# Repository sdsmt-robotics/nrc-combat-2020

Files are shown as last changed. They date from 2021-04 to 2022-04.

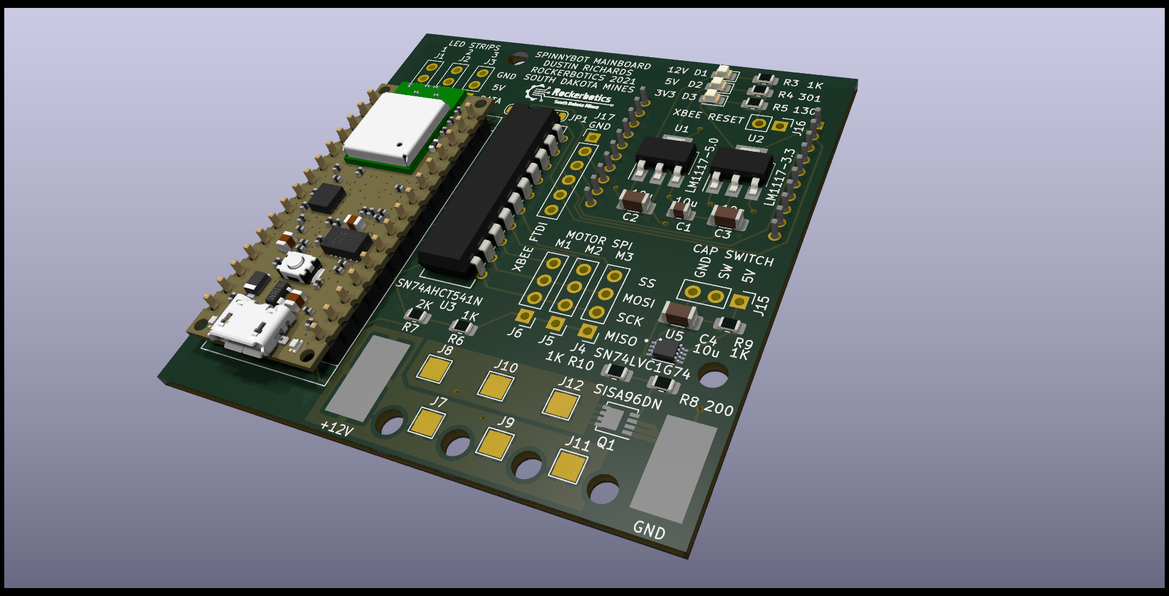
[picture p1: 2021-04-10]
spinnybot-motherboad/spinnybot-motherboad.png

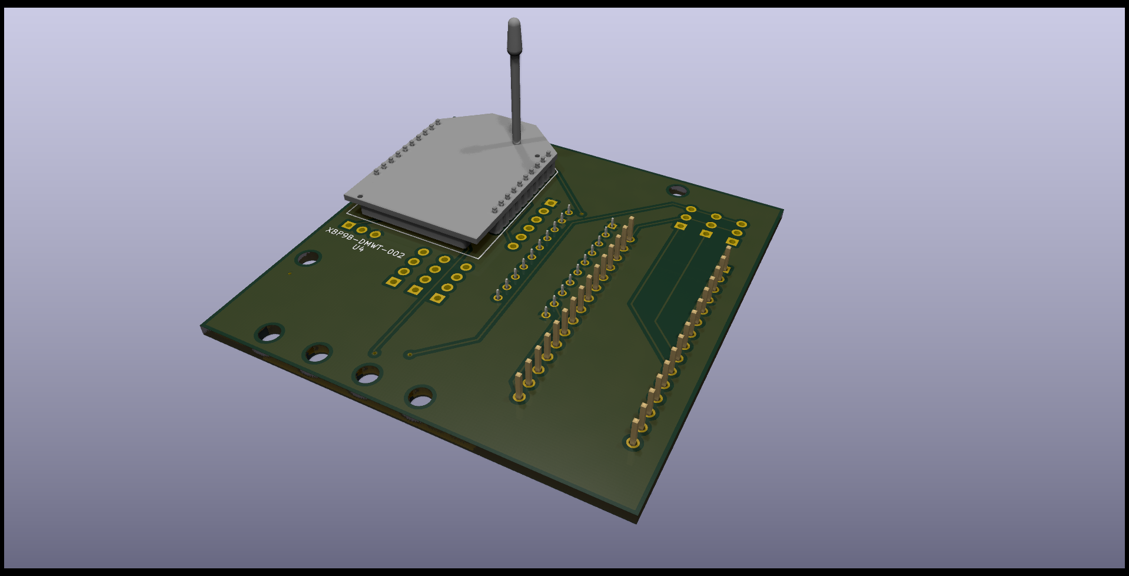
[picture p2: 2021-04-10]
spinnybot-motherboad/spinnybot-motherboad2.png

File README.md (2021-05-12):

# nrc-combat-2020
Robot code for the NRC Combat competition bot. Information about this bot can be found here: http://robotics.sdsmt.edu/projects/spinnybot  

# Hardware Info
This code is meant to run on an ESP32. It uses an ICM20649 Wide-Range 6-DoF IMU for orientation sensing. It also controls three NeoPixel 8x5050 RGB LED Sticks. For motor control, it interfaces with three Nidec24h motors controlled by our custom motor controller boards. For remote control, the bot receives commands from our custom remote controls over an xBee. The full system diagram is shown below.  

  

The main components of the control system (ESP32, xBee, voltage regulators, level shifters, etc) are held on a custom main board. The Kicad files for this are in the [spinnybot-motherboard](https://github.com/sdsmt-robotics/nrc-combat-2020/tree/master/spinnybot-motherboad) folder.  

# Software Info  
The main code for the bot is found in the [spinnybot-code](https://github.com/sdsmt-robotics/nrc-combat-2020/tree/master/spinnybot-code) folder. There are some additional arduino sketches for testing the various functionallities. These are found in the "testing" sub-folder. These tests run with the same libraries as the main control code.  

The pinouts are set up to run with the ESP32. But it should be able to run on any device with similar pin functionalities.  

## Required Libraries  
The required libraries are as follows:  
* Nidec24hController.h - Interface lib for the motor speed controller. Found [here](https://github.com/sdsmt-robotics/MotorSpeedController/tree/master/Software/controllerInterfaceLib).  
* Controller.h - Receive library for our custom remote control. Found [here](https://github.com/sdsmt-robotics/MotorSpeedController/tree/master/Software/controllerInterfaceLib).  
* FastLED.h - Code for interfacing with the LED strips. Install through the Arduino library manager.  
* Adafruit_ICM20649.h - Library for the ICM-20649 IMU. Install through the Arduino library manager.  

## Functionality  
The functionality is as follows. First, the bot will first initialize all peripherals. The LED strips are initialized first to show status throughout.Then the IMU is initialized. While this is occurring, the bot MUST remain stationary. The code runs through a calibration sequence each time, and any bumps will cause issues. During this stage the LEDs will show yellow, and will go green once complete. After, this the motors and remote control communications will be set up as well.  

For the main control loop, the bot has three main states:  
* No-spin: lights will be purple and the bot will not be spinning. Driver can drive the bot around with standard controls.  
* Spinny: bot is spinning with IMU feedback for orientation. LEDs will be red except when facing forward at which point they will be blue. Controls for driving are relative to "forward".  
* Full-spinny: lights will be red and bot will set all motors to full power. Feedback from IMU and attempts to drive will be ignored.

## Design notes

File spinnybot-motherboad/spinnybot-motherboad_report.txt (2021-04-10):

PCB statistics report
=====================
- Date: 3/25/2021 2:41:33 AM
- Project: spinnybot-motherboad
- Board name: spinnybot-motherboad

Board
-----
- Width: 63.5000 mm
- Height: 63.5000 mm
- Area: 4032.2500 sq. mm

Pads
----
- Through hole: 102
- SMD: 69
- Connector: 0
- NPTH: 6

Vias
----
- Through vias: 10
- Blind/buried: 0
- Micro vias: 0

Components
----------

| | Front Side | Back Side | Total |
|---|---|---|---|
|THT: | 12  | 1  | 13  |
|SMD: | 23  | 0  | 23  |
|Total:  | 35  | 1  | 36  |
| | | | |

Drill holes
-----------

| Count | Shape | X Size | Y Size | Plated | Via/Pad | Start Layer | Stop Layer |
|---|---|---|---|---|---|---|---|
| 186 | Round | 1.0000 mm | 1.0000 mm | PTH | Pad | F.Cu | B.Cu |
| 60 | Round | 0.7874 mm | 0.7874 mm | PTH | Pad | F.Cu | B.Cu |
| 60 | Round | 0.8000 mm | 0.8000 mm | PTH | Pad | F.Cu | B.Cu |
| 30 | Round | 0.4000 mm | 0.4000 mm | PTH | Via | F.Cu | B.Cu |
| 18 | Round | 3.0000 mm | 3.0000 mm | NPTH | Pad | F.Cu | B.Cu |

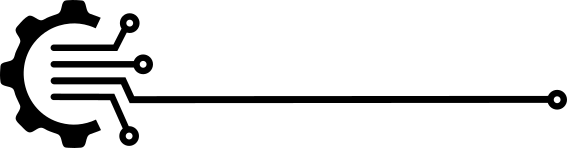
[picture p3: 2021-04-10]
spinnybot-motherboad/art6/.svg2shenzhen-cache/images/F.Mask_g1609.png

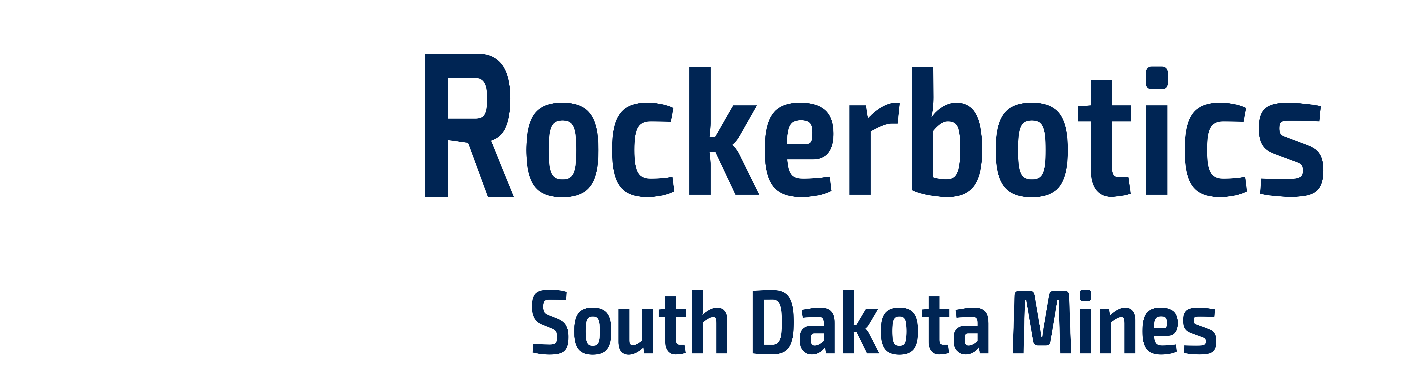
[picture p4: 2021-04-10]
spinnybot-motherboad/art4/.svg2shenzhen-cache/images/F.SilkS_layer2.png

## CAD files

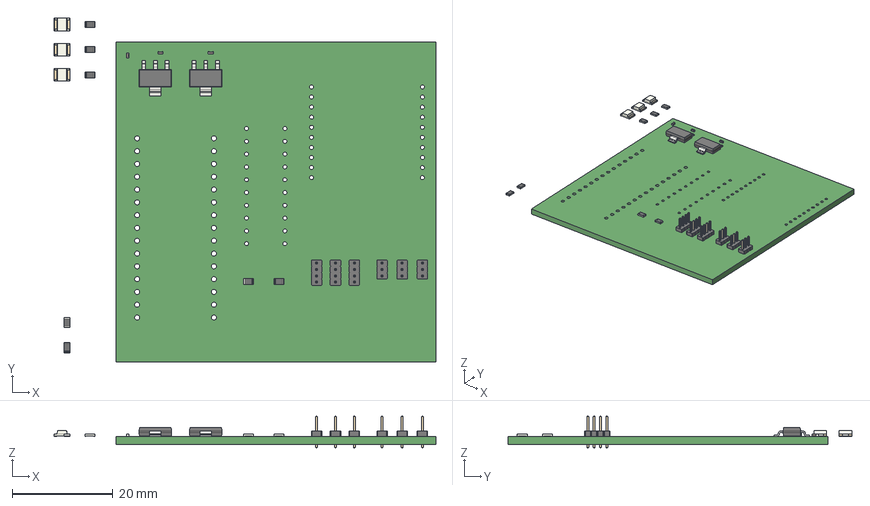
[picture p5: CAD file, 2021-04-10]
spinnybot-motherboad/spinnybot-motherboad.step
75.8 x 68.2 x 6.30 mm

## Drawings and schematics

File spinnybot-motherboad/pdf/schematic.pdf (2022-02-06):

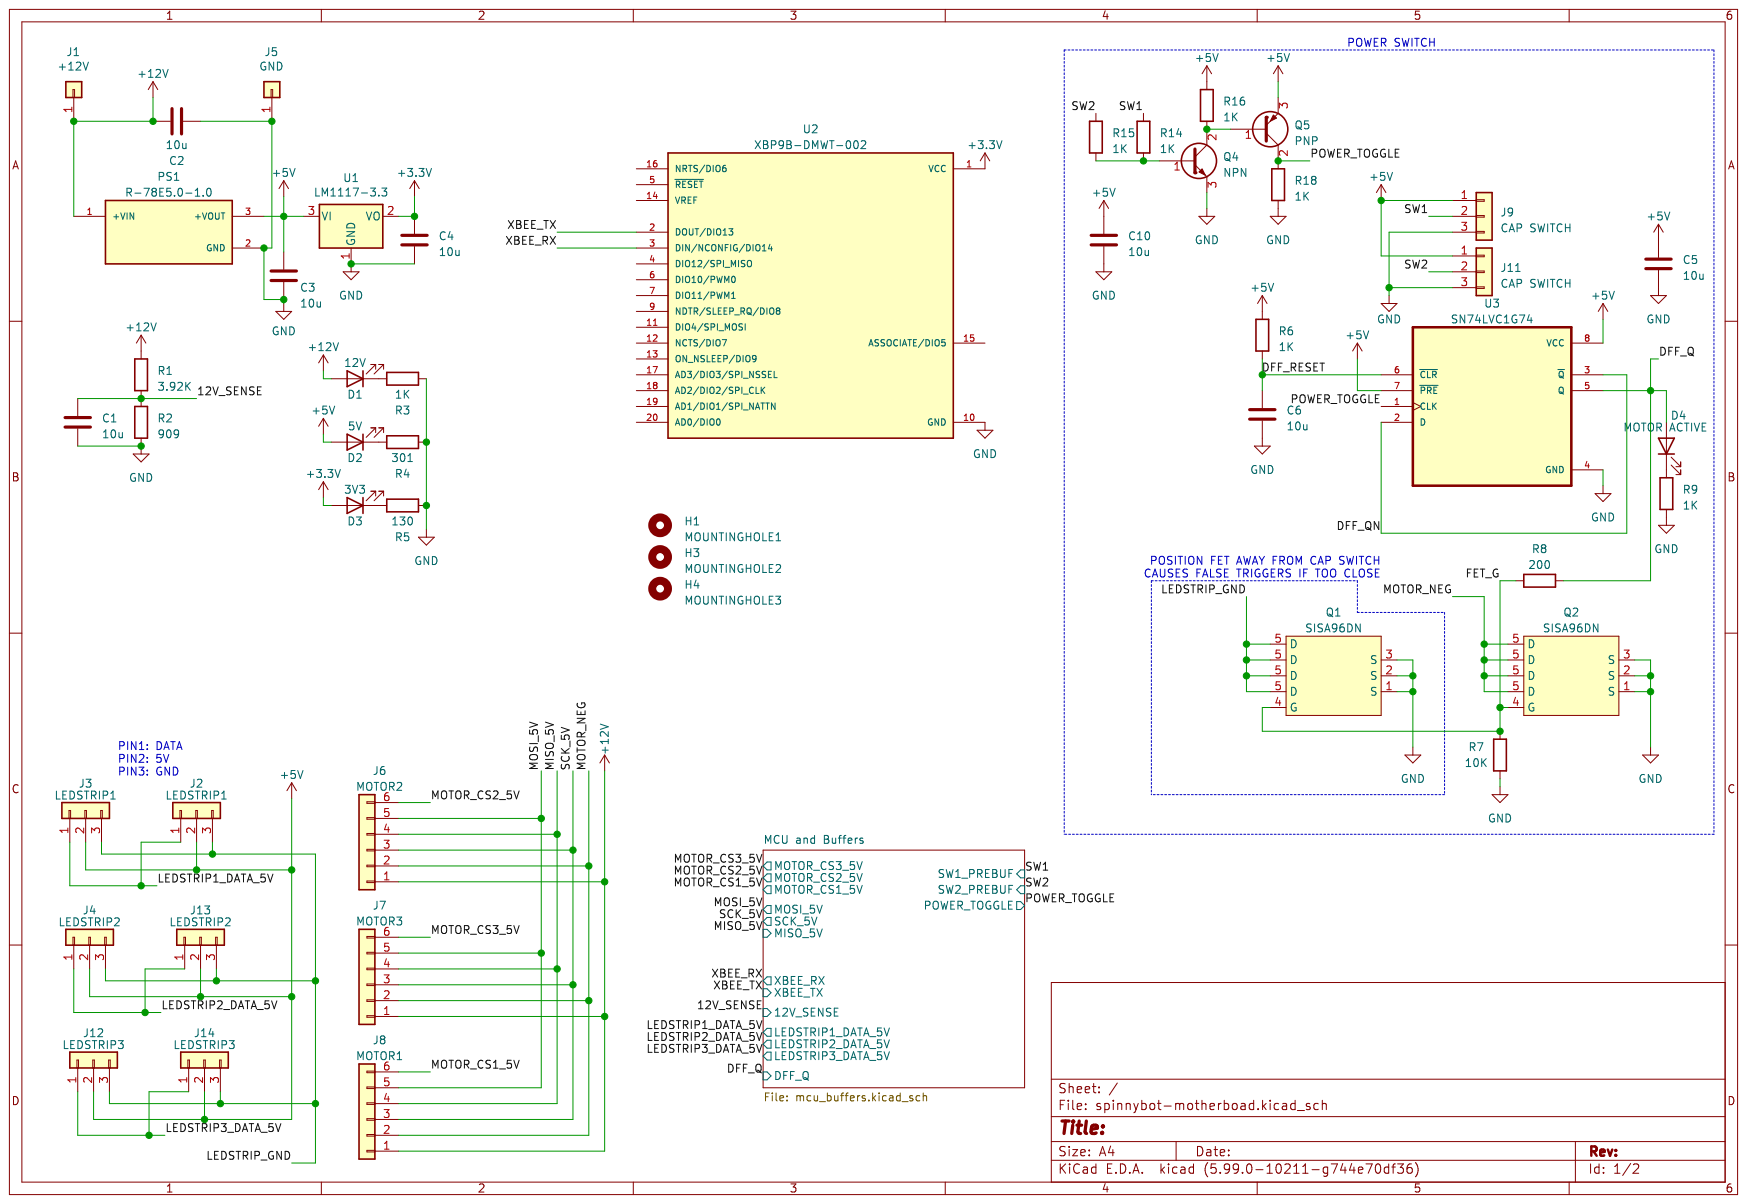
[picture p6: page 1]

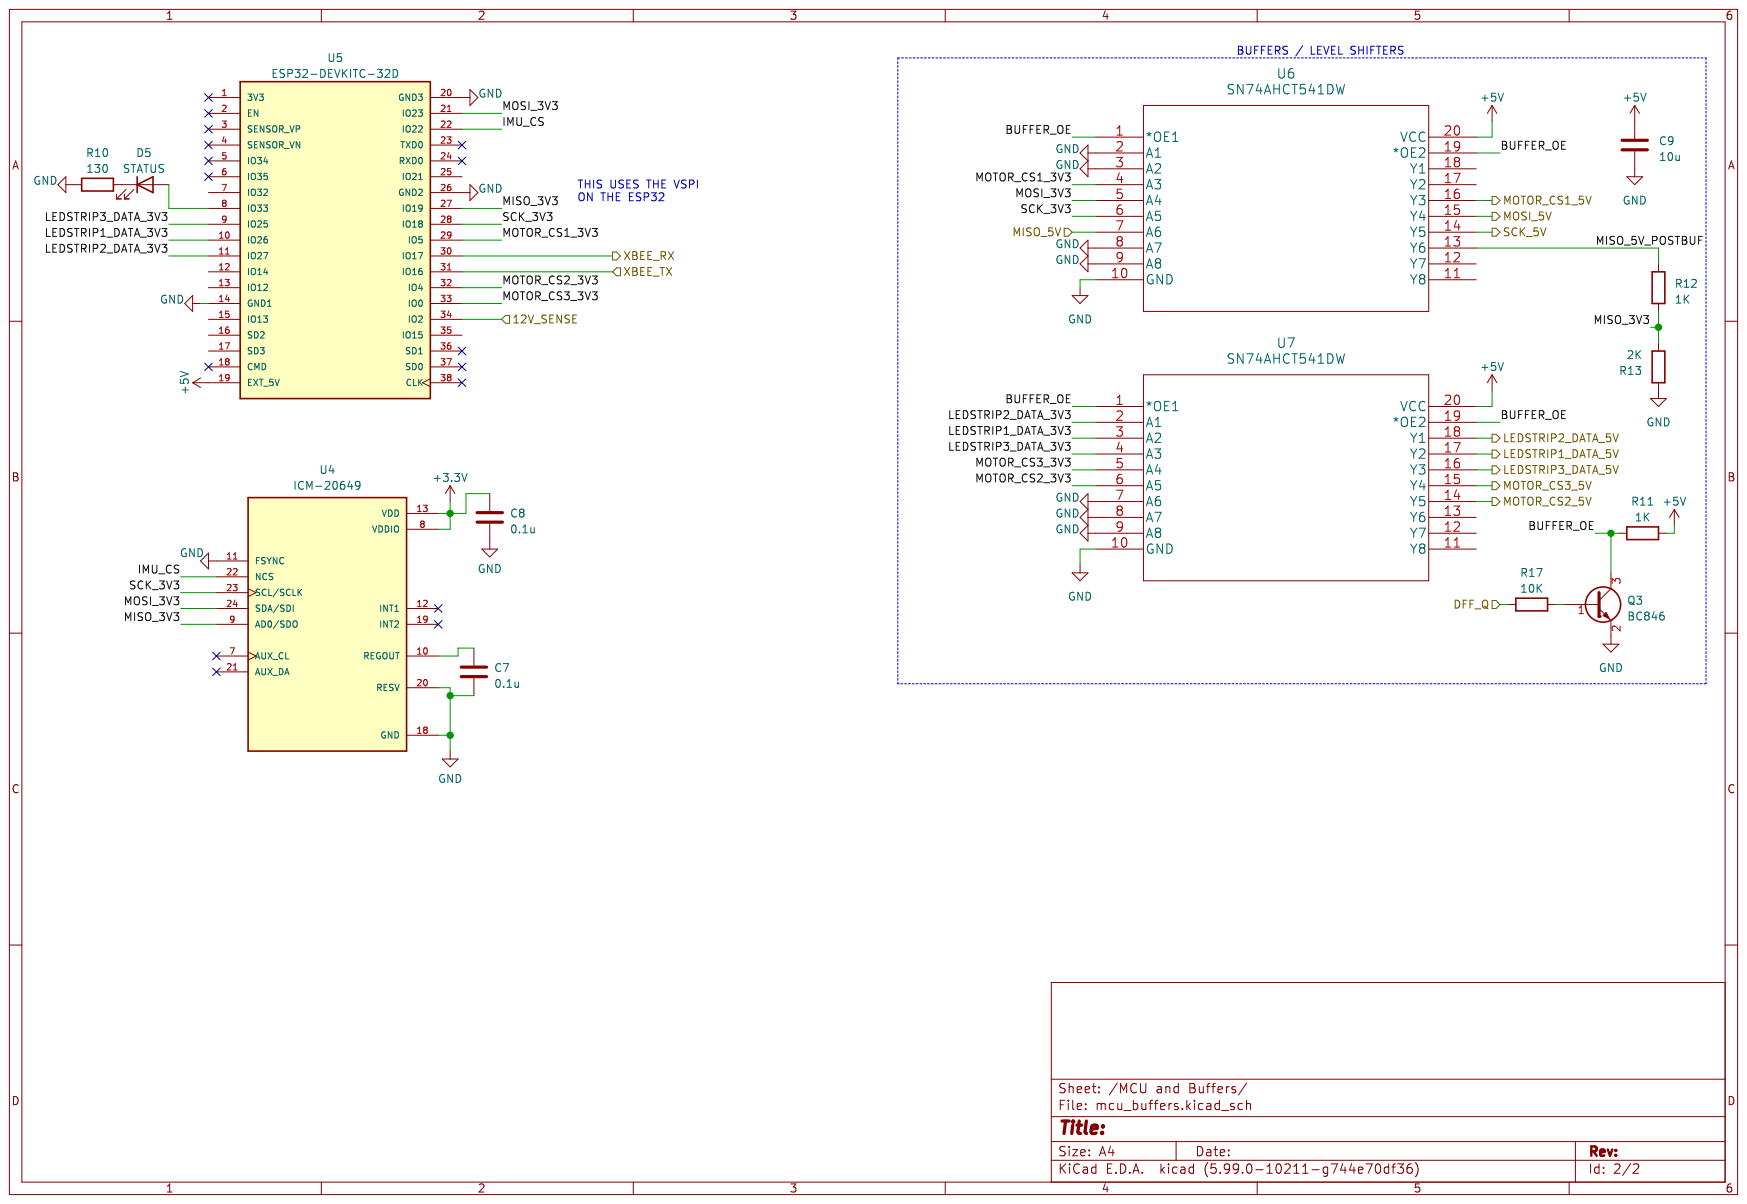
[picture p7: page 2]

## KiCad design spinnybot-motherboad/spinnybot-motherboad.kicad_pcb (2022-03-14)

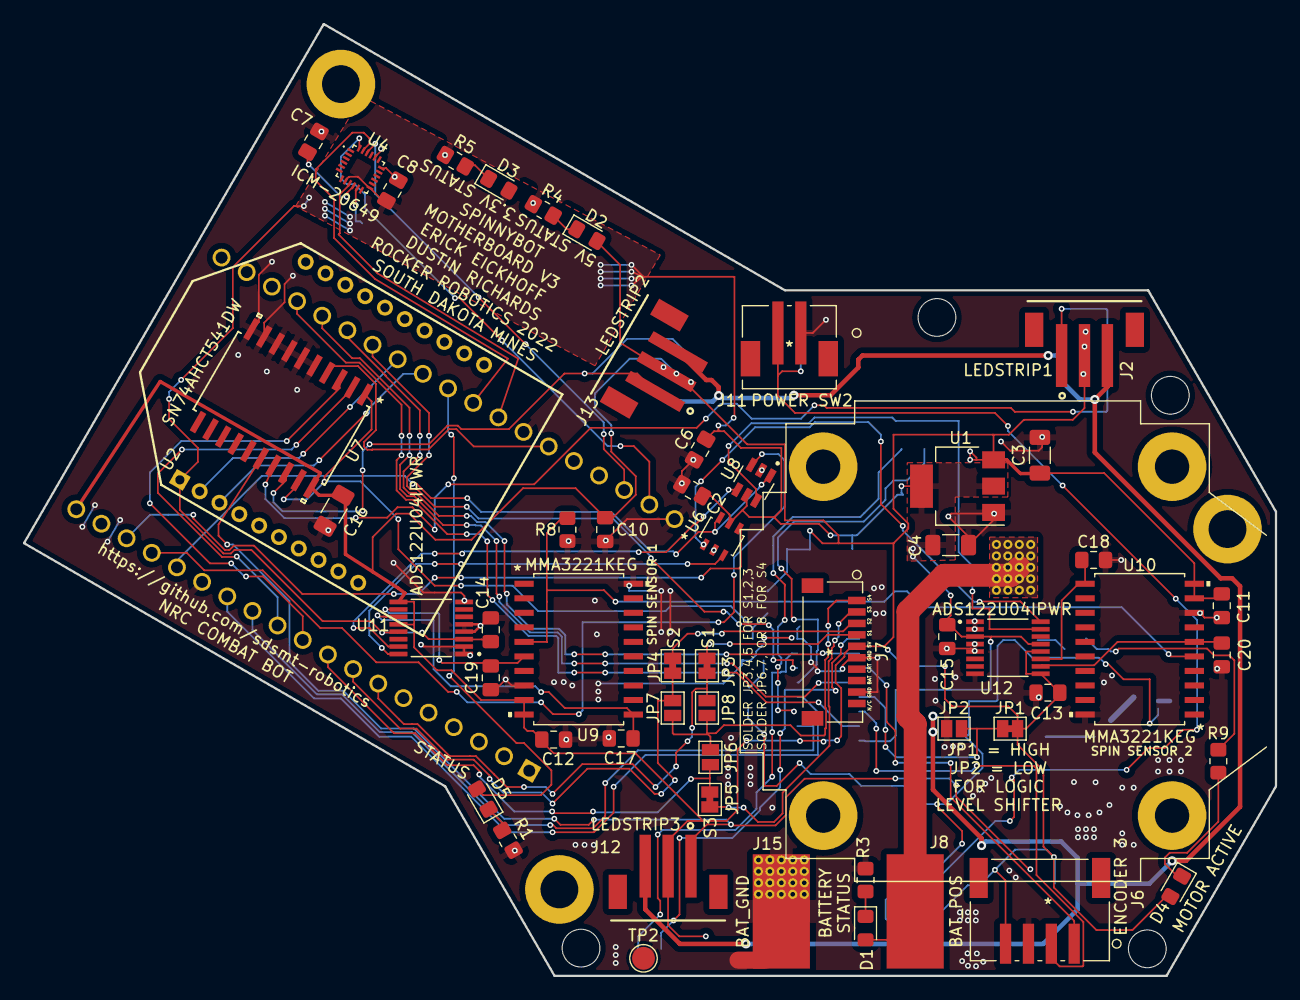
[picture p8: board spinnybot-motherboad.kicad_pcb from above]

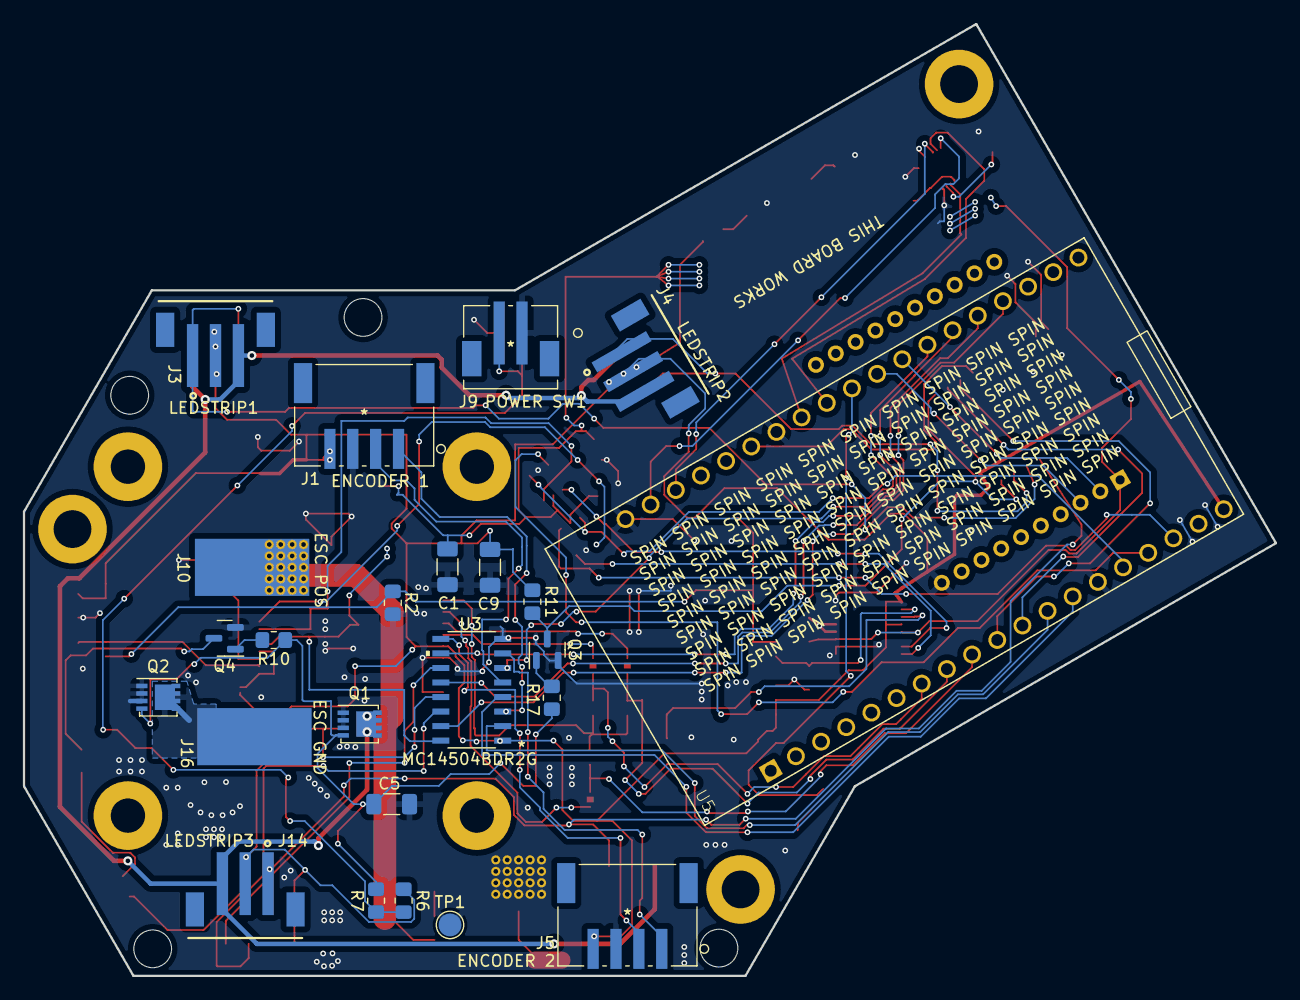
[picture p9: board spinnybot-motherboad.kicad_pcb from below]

Board: 2 copper layers, 109.4 x 83.2 mm, 87 parts (24 on the bottom side), 63 nets.

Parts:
A1: ESC_Hobbywing_X-Rotor_Micro_60A_4in1
C1, C3, C4, C5, C9: 10u; C_1206_3216Metric_Pad1.33x1.80mm_HandSolder
C2, C6, C7, C8, C10, C11, C12, C13, C14, C15: 0.1u; C_0805_2012Metric_Pad1.18x1.45mm_HandSolder
C16: 0.1u; C_1206_3216Metric_Pad1.33x1.80mm_HandSolder
C17, C18, C19, C20: 10nF; C_0805_2012Metric_Pad1.18x1.45mm_HandSolder
D1: 12V; LED_0805_2012Metric_Pad1.15x1.40mm_HandSolder
D2: 5V; LED_0805_2012Metric_Pad1.15x1.40mm_HandSolder
D3: 3V3; LED_0805_2012Metric_Pad1.15x1.40mm_HandSolder
D4: MOTOR ACTIVE; LED_0805_2012Metric_Pad1.15x1.40mm_HandSolder
D5: STATUS; LED_0805_2012Metric_Pad1.15x1.40mm_HandSolder
H1: MOUNTINGHOLE1; MountingHole_3.3mm
H2, H7: STRAINHOLE1; StrainHole_3.3mm
H3: MOUNTINGHOLE2; MountingHole_3.3mm
H4: MOUNTINGHOLE3; MountingHole_3.3mm
H6: STRAINHOLE3; StrainHole_3.3mm
H8: STRAINHOLE2; StrainHole_3.3mm
J1: ENCODER 1; S4B-PH-SM4-TBLFSN
J2, J3: LEDSTRIP1; JST_B3B-PH-SM4-TB(LF)(SN)
J4, J13: LEDSTRIP2; JST_B3B-PH-SM4-TB(LF)(SN)
J5: ENCODER 2; S4B-PH-SM4-TBLFSN
J6: ENCODER 3; S4B-PH-SM4-TBLFSN
J7: SM10B-SRSS-TB
J8: BAT_POS; SolderWirePad_1x01_SMD_5x10mm
J9: POWER SW1; B2B-PH-SM4-TBLFSN
J10: ESC_POS; Stitched_SolderWirePad_1x01_SMD_5x10mm
J11: POWER SW2; B2B-PH-SM4-TBLFSN
J12, J14: LEDSTRIP3; JST_B3B-PH-SM4-TB(LF)(SN)
J15: BAT_GND; Stitched_SolderWirePad_1x01_SMD_5x10mm
J16: ESC_GND; SolderWirePad_1x01_SMD_5x10mm
JP1, JP3, JP4, JP5: SolderJumper_2_Bridged; SolderJumper-2_P1.3mm_Bridged_Pad1.0x1.5mm
JP2, JP6, JP7, JP8: SolderJumper_2_Open; SolderJumper-2_P1.3mm_Open_Pad1.0x1.5mm
Q1, Q2: SISA96DN; Vishay_PowerPAK_1212-8_Single
Q3, Q4: BC846; SOT-23
R1, R5: 130; R_0805_2012Metric_Pad1.20x1.40mm_HandSolder
R2, R8: 10k; R_0805_2012Metric_Pad1.20x1.40mm_HandSolder
R3, R11: 1K; R_0805_2012Metric_Pad1.20x1.40mm_HandSolder
R4: 301; R_0805_2012Metric_Pad1.20x1.40mm_HandSolder
R6: 1k; R_0805_2012Metric_Pad1.20x1.40mm_HandSolder
R7: 150k; R_0805_2012Metric_Pad1.20x1.40mm_HandSolder
R9: 220; R_0805_2012Metric_Pad1.20x1.40mm_HandSolder
R10, R17: 10K; R_0805_2012Metric_Pad1.20x1.40mm_HandSolder
TP1, TP2: TestPoint; TestPoint_Pad_D2.0mm
U1: LM1117-3.3; SOT-223-3_TabPin2
U2: XBP9B-DMWTB002; DIP2200W51P200L3294H279Q20P
U3: MC14504BDR2G
U4: ICM-20649; QFN40P300X300X95-24N
U5: ESP32-DEVKITC-32D; MODULE_ESP32-DEVKITC-32D
U6: 74LVC1G157GV_125
U7: SN74AHCT541DW
U8: SN74LVC1G18DBVR; SOT95P280X145-6N
U9, U10: MMA3221KEG
U11, U12: ADS122U04IPWR; SOP65P640X120-16N

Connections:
+3V3: C1.1, C2.1, C4.1, C6.1, C8.1, C14.1, C15.1, D3.2 (A), U1.2 (VO), U2.1 (VCC), U3.16 (VDD), U4.8 (VDDIO), U4.13 (VDD), U6.5 (VCC), U8.5 (VCC), U11.3 (RESET_N), U11.13 (DVDD), U12.3 (RESET_N), U12.13 (DVDD)
+5V: C3.1, C9.1, C10.1, C11.1, C12.1, C13.1, C16.1, D2.2 (A), D4.2 (A), J1.4, J2.2, J3.2, J4.2, J5.4, J6.4, J7.5, J12.2, J13.2, J14.2, JP1.2 (B), R6.1, R11.1, U1.3 (VI), U3.1 (VCC), U5.19 (EXT_5V), U7.20 (VCC), U9.9 (VDD), U9.10 (AVDD), U10.9 (VDD), U10.10 (AVDD), U11.9 (REFP), U11.12 (AVDD), U12.9 (REFP), U12.12 (AVDD)
+12V: D1.2 (A), J8.1, J10.1
/ACCEL_SELF_TEST: R2.1, R8.1, U9.5 (ST), U10.5 (ST)
/ADC_RX: U5.17 (SD3), U6.4 (Y)
/ADC_SEL: U5.15 (IO13), U6.6 (S), U8.1 (S)
/ADC_TX: U5.16 (SD2), U8.3 (A)
/Connectors/ESC_S4: J7.1, JP6.1 (A), JP7.1 (A), JP8.1 (A)
/ENC_1A_5V: J1.1, U3.3 (AIN)
/ENC_1B_5V: J1.2, U3.5 (BIN)
/ENC_2A_5V: J5.1, U3.7 (CIN)
/ENC_2B_5V: J5.2, U3.9 (DIN)
/ENC_3A_5V: J6.1, U3.11 (EIN)
/ENC_3B_5V: J6.2, U3.14 (FIN)
/ESC_S1: JP3.2 (B), JP8.2 (B), U5.7 (IO32)
/ESC_S2: JP4.2 (B), JP7.2 (B), U5.8 (IO33)
/ESC_S3: JP5.2 (B), JP6.2 (B), U5.9 (IO25)
/IMU and Accelerometers/ADC1_RX: U6.3 (I0), U11.16 (RX)
/IMU and Accelerometers/ADC1_TX: U8.4 (Y1), U11.15 (TX)
/IMU and Accelerometers/ADC2_RX: U6.1 (I1), U12.16 (RX)
/IMU and Accelerometers/ADC2_TX: U8.6 (Y2), U12.15 (TX)
/IMU_CS: U4.22 (NCS), U5.22 (IO22)
/LEDSTRIP1_DATA_5V: J2.1, J3.1, U7.17 (Y2)
/LEDSTRIP2_DATA_5V: J4.1, J13.1, U7.18 (Y1)
/LEDSTRIP3_DATA_5V: J12.1, J14.1, U7.16 (Y3)
/LEDSTRIP_GND: J2.3, J3.3, J4.3, J12.3, J13.3, J14.3, Q1.5 (D)
/MCU and Buffers/BUFFER_OE: Q3.3 (C), R11.2, U7.1 (*OE1), U7.19 (*OE2)
/MCU and Buffers/ENC_1A_3V3: U3.2 (AOUT), U5.12 (IO14)
/MCU and Buffers/ENC_1B_3V3: U3.4 (BOUT), U5.13 (IO12)
/MCU and Buffers/ENC_2A_3V3: U3.6 (COUT), U5.32 (IO4)
/MCU and Buffers/ENC_2B_3V3: U3.10 (DOUT), U5.33 (IO0)
/MCU and Buffers/ENC_3A_3V3: U3.12 (EOUT), U5.34 (IO2)
/MCU and Buffers/ENC_3B_3V3: U3.15 (FOUT), U5.35 (IO15)
/MCU and Buffers/LEDSTRIP1_DATA_3V3: U5.10 (IO26), U7.3 (A2)
/MCU and Buffers/LEDSTRIP2_DATA_3V3: U5.11 (IO27), U7.2 (A1)
/MCU and Buffers/LEDSTRIP3_DATA_3V3: U5.25 (IO21), U7.4 (A3)
/MCU and Buffers/XBEE_RX: U2.3 (DIN/NCONFIG/DIO14), U5.30 (IO17)
/MCU and Buffers/XBEE_TX: U2.2 (DOUT/DIO13), U5.31 (IO16)
/MISO_3V3: U4.9 (AD0/SDO), U5.27 (IO19)
/MOSI_3V3: U4.24 (SDA/SDI), U5.21 (IO23)
/POWER_ON: C5.2, Q1.4 (G), Q2.4 (G), R7.2, R10.1, R17.2
/Power/ESC_GND: J16.1, Q2.5 (D)
/Power/POWER_SW_IN: J9.2, J11.2, R6.2, R7.1
/SCK_3V3: U4.23 (SCL/SCLK), U5.28 (IO18)
GND: C1.2, C2.2, C3.2, C4.2, C5.1, C6.2, C7.2, C8.2, C9.2, C10.2, C11.2, C12.2, C13.2, C14.2, C15.2, C16.2, C17.2, C18.1, C19.1, C20.1, J1.3, J5.3, J6.3, J7.6, J7.9, J9.1, J11.1, J15.1, JP2.1 (A), Q1.1 (S), Q1.2 (S), Q1.3 (S), Q2.1 (S), Q2.2 (S), Q2.3 (S), Q3.2 (E), Q4.2 (E), R1.1, R2.2, R3.1, R4.1, R5.1, R8.2, TP1.1, TP2.1, U1.1 (GND), U2.10 (GND), U3.8 (VSS), U4.11 (FSYNC), U4.18 (GND), U4.20 (RESV), U5.14 (GND1), U5.20 (GND3), U5.26 (GND2), U6.2 (GND), U7.5 (A4), U7.6 (A5), U7.7 (A6), U7.8 (A7), U7.9 (A8), U7.10 (GND), U8.2 (GND), U9.8 (VSS), U9.20 (GND), U10.8 (VSS), U10.20 (GND), U11.1 (GPIO1), U11.2 (GPIOO), U11.4 (DGND), U11.5 (AVSS), U11.8 (REFN), U12.1 (GPIO1), U12.2 (GPIOO), U12.4 (DGND), U12.5 (AVSS), U12.8 (REFN)
unnamed: C7.1, U4.10 (REGOUT)
unnamed: C17.1, U9.11 (YOUT), U11.11 (AINO)
unnamed: C18.2, U10.11 (YOUT), U12.11 (AINO)
unnamed: C19.2, U9.6 (XOUT), U11.10 (AIN1)
unnamed: C20.2, U10.6 (XOUT), U12.10 (AIN1)
unnamed: D1.1 (K), R3.2
unnamed: D2.1 (K), R4.2
unnamed: D3.1 (K), R5.2
unnamed: D4.1 (K), R9.2
unnamed: D5.1 (K), R1.2
unnamed: D5.2 (A), U5.29 (IO5)
unnamed: J7.2, JP5.1 (A)
unnamed: J7.3, JP4.1 (A)
unnamed: J7.4, JP3.1 (A)
unnamed: JP1.1 (A), JP2.2 (B), U3.13 (MODE)
unnamed: Q3.1 (B), R17.1
unnamed: Q4.1 (B), R10.2
unnamed: Q4.3 (C), R9.1

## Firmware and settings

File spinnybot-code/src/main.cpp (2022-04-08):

#include <Arduino.h>
#include <math.h>

// #include "accelerometer.h"
#include "constants.h"
#include "controller.h"
#include "driveFuncs.h"
#include "encoder.h"
#include "imu.h"
#include "led.h"
#include "motor.h"
#include "ota.h"
#include "pins.h"
#include "utility.h"

#define AP_SSID "SPINNY" // ssid for robot

// ---- SENSOR STUFF ----

IMU imu;

Encoder e1(ENC_1, 360);
Encoder e2(ENC_2, 360);
Encoder e3(ENC_3, 360);

/* Accelerometers accel(Serial1, ADC_SELECT, ADC_TX,
                     ADC_RX); // note: tx and rx are fliped
                     */

// ---- LED STUFF ----

LedStrip strip1(LED_STRIP_1);
LedStrip strip2(LED_STRIP_2);
LedStrip strip3(LED_STRIP_3);
LedStrip* strips[] = {&strip1, &strip2, &strip3};

// ---- MOTOR STUFF ----

Motor m1(MOTOR_1, MOTOR_1_RMT_CHANNEL);
Motor m2(MOTOR_2, MOTOR_2_RMT_CHANNEL);
Motor m3(MOTOR_3, MOTOR_3_RMT_CHANNEL);

const long MOTOR_UPDATE_INTERVAL = 10; // motor update loop time in microseconds
long last_motor_update = micros();

// ---- LOOP STUFF ----

bool robot_enabled = false;

const long LOOP_INTERVAL = 1000; // microsec
long last_loop = micros();

// ---- CONTROLLER STUFF ----

Controller controller(CONTROLLER_SERIAL);

// movement
// range -1 to 1, negative is reverse
float x = 0;
float y = 0;

// Offset for facing direction, FIXME need values for offset
float imu_offset = 0;

// spin speed
//  range -1 to 1, negative is reverse
float spin = 0;

bool flip = false;

bool full_send = false;

// variables

float body_angle = 0;

DriveManager driveManager;

// ---- SENSOR FUNCTIONS ----

/**
   @brief Initializes all sensors.
*/
void initSensors() {
  // init IMU
  if (!imu.init()) {
    Serial.println("\nimu fail init");
  }

  // init accelerometers
  // accel.init();

  // init encoders
  e1.init();
  e2.init();
  e3.init();
}

/**
   @brief Updates all sensors.
*/
void updateSensors() {
  // update IMU
  imu.update();

  // update accelerometers
  // accel.update();

  // update encoders
  e1.update();
  e2.update();
  e3.update();

  // Update values in drive manager
  float encVels[] = {e1.getUnfilteredSpeed(), e2.getUnfilteredSpeed(), e3.getUnfilteredSpeed()};
  driveManager.updateOrientation(imu.getRawVelocity(), encVels);

  //body_angle = imu.getAngle() + imu_offset;
}

// ---- MOTOR FUNCTIONS ----

/**
   @brief Initializes all motors.
*/
void initMotors() {
  m1.init();
  m2.init();
  m3.init();
}

/**
   @brief Sends a DShot command to all motors.
   @param cmd command
*/
void sendAllMotorCommand(int cmd) {
  m1.send_dshot_command(cmd);
  m2.send_dshot_command(cmd);
  m3.send_dshot_command(cmd);
}

/**
   @brief Sets a power for all motors.
   @param power power value to set. -1000 to 1000
*/
void sendAllMotorPower(int power) {
  m1.set_speed_signed(power);
  m2.set_speed_signed(power);
  m3.set_speed_signed(power);
}

/**
   @brief Arms all motors by initialy sending the 0 command and then sets the
   power to 0 for the initialization. This blocks for MOTOR_INIT_TIME
   miliseconds.
*/
void armMotors() {
  long init_motor_start = millis();
  sendAllMotorCommand(0);
  while (millis() - init_motor_start < MOTOR_INIT_TIME) {
    sendAllMotorPower(0);
  }
}

/**
   @brief Updates drive motor powers with control and angle inputs.
   @param spin Spin speed modifier. -1.0 to 1.0
   @param x X direction movement modifier. -1.0 to 1.0
   @param y Y direction movement modifier. -1.0 to 1.0
   @param angle Current angle of robot in radians
*/
void updateDrive(float spin, float x, float y) {
  // Calculate the power
  int power[3] = {0, 0, 0};
  driveManager.calcDrivePower(power, spin, x, y);

  // update motor power
  m1.set_speed_signed(power[0]);
  m2.set_speed_signed(power[1]);
  m3.set_speed_signed(power[2]);
}

// ---- LED FUNCTIONS ----

/**
   @brief Turns both status LEDs on and off
   @param on true = on, false = off
*/
void setStatusLED(bool on) {
  digitalWrite(STATUS_LED_PIN, on);
  digitalWrite(ESP_STATUS_LED_PIN, on);
}

/**
   @brief Initializes all LED strips.
*/
void initLEDStrips() {
  strip1.init();
  strip2.init();
  strip3.init();
}

/**
 * @brief Sets up and initializes LED strips and status LED
 */
void initLEDs() {
  pinMode(STATUS_LED_PIN, OUTPUT);
  pinMode(ESP_STATUS_LED_PIN, OUTPUT);

  setStatusLED(false);

  initLEDStrips();
}

/**
   @brief Updates all LED strips to set colors.
*/
void showLEDStrips() {
  strip1.show();
  strip2.show();
  strip3.show();
}

/**
   @brief Updates all LED strip brightnesses.
*/
void setLEDStripBrightness(uint8_t b) {
  strip1.setBrightness(b);
  strip2.setBrightness(b);
  strip3.setBrightness(b);
}

/**
   @brief Sets all LED strips to RGB color.
   @param red red 0 to 255
   @param green red 0 to 255
   @param blue red 0 to 255
*/
void fillLEDs(uint8_t red, uint8_t green, uint8_t blue) {
  strip1.fillColor(strip1.makeColor(red, green, blue));
  strip2.fillColor(strip2.makeColor(red, green, blue));
  strip3.fillColor(strip3.makeColor(red, green, blue));
}

void updateStrips(uint32_t color) {
  const float OFFSETS[] = {-PI / 3, PI / 3, PI};
  const static float angle_range = PI / 12;

  float norm_angle = driveManager.getCurAngle();

  // Iterate through strips and set values
  for (int i = 0; i < 3; i++) {
    // Flip the offset for the strip if the bot is flipped
    float offset = (flip ? -1 : 1) * OFFSETS[i];

    // Set the color
    if (abs(normalizeAngle(norm_angle + offset)) < angle_range) {
      strips[i]->fillColor(color);
    } else {
      strips[i]->fillColor(LedStrip::makeColor(0, 0, 0));
    }
  }
}

// ---- MAIN FUNCTIONS ----

void setup() {

  Serial.begin(115200);

  // Initialize the access point and OTA udpater
  Serial.print("Initializing AP...");
  bool success = initAp(AP_SSID);
  Serial.println(success ? "done!" : "fail.");
  if (success) {
    Serial.print("Initializing OTA...");
    initOta();
    Serial.println("Ready!");
  }

  initLEDs();

  // set LED strips to red
  fillLEDs(255, 0, 0);
  showLEDStrips();

  controller.init();
  controller.setJoyDeadzone(0.1);

  initSensors();
  initMotors();

  // set LED strips to yellow
  fillLEDs(255, 255, 0);
  showLEDStrips();

  armMotors();

  // set LED strips to green
  fillLEDs(0, 255, 0);
  showLEDStrips();
}

void loop() {
  // main loop timer
  if (micros() - last_loop > LOOP_INTERVAL) {
    last_loop = micros();

    // update controls
    if (controller.connected()) {

      // turn status on and set LED strips to green
      setStatusLED(true);
      fillLEDs(0, 255, 0);

      if (controller.buttonClick(RIGHT)) {
        robot_enabled = true;
        spin = 0.1;
        Serial.println("run");
      }
      if (controller.buttonClick(LEFT)) {
        spin = 0;
        robot_enabled = false;
        Serial.println("stop");
      }

      x = -controller.joystick(RIGHT, X); // For some stupid reason, the x-axis is inverted.
      y = controller.joystick(RIGHT, Y);

      // "Rotate". Limit rotation rate to 100deg/s.
      static unsigned long lastAngleChange = millis();
      if (millis() - lastAngleChange > 10) {
        driveManager.rotate(DEG_TO_RAD * controller.joystick(LEFT, X));
        lastAngleChange = millis();
      }

      // gyro drift comensation
      // Robot rotates at ~500rpm = 52 rad/s. 
      if (controller.dpadClick(RIGHT) && robot_enabled) {
        driveManager.adjustDrift(0.8);
      }
      if (controller.dpadClick(LEFT) && robot_enabled) {
        driveManager.adjustDrift(-0.8);
      }

      if (controller.dpadClick(UP) && robot_enabled) {
        spin += 0.1;
        if (spin > 1.0) {
          spin = 1.0;
        }
        Serial.println("spin up");
        Serial.println(spin);
      }

      if (controller.dpadClick(DOWN) && robot_enabled) {
        spin -= 0.1;
        if (spin < 0.1) {
          spin = 0.1;
        }
        Serial.println("spin down");
        Serial.println(spin);
      }

      if (controller.dpadClick(LEFT) && !robot_enabled) {
        flip = false;
        Serial.println("spin normal");
      }

      if (controller.dpadClick(RIGHT) && !robot_enabled) {
        flip = true;
        Serial.println("spin reverse");
      }

      if (controller.button(DOWN)) {
        Serial.print("angle: \t");
        Serial.print((driveManager.getCurAngle() * RAD_TO_DEG));
        Serial.println();
      }

      if (controller.button(UP)) {
        Serial.print("accel: \t");
        Serial.print("");
        Serial.println();
      }

      if (controller.bumper(RIGHT) && robot_enabled) {
        full_send = true;
        Serial.println("FULL SEND!!!");
      } else {
        full_send = false;
      }

      // re-arm motors when power is reapplyed
      if (controller.joyButtonClick(LEFT)) {
        // set LED strips to yellow
        fillLEDs(255, 255, 0);
        showLEDStrips();

        // arm sequence
        armMotors();

        // set LED strips to green
        fillLEDs(0, 255, 0);
        showLEDStrips();
      }

    } else {

      // controller disconnected

      // set status to off and all LED strips to red
      setStatusLED(false);
      fillLEDs(255, 0, 0);

      // disable robot
      robot_enabled = false;
    }

    updateSensors();
  }

  // motor update timer
  if (micros() - last_motor_update > MOTOR_UPDATE_INTERVAL) {
    last_motor_update = micros();

    if (robot_enabled) {

      // run motors
      if (!full_send) {
        updateDrive(spin, x, y);

        // set led strips to purple
        updateStrips(LedStrip::PURPLE);

      } else {
        // full send mode
        if (flip) {
          sendAllMotorPower(-FULL_SEND_POWER);
        } else {
          sendAllMotorPower(FULL_SEND_POWER);
        }
        // set led strips to red
        fillLEDs(255, 0, 0);
      }

    } else {
      // robot disabled. stop all motors
      sendAllMotorPower(0);
    }
    showLEDStrips();
  }
}

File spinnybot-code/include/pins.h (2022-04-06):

/**
 * File to define the pins used by the various devices.
 */

#ifndef __BB_PINS__
#define __BB_PINS__

// ---- PINS ----

#define STATUS_LED_PIN 5
#define ESP_STATUS_LED_PIN 2 // internal led on esp32 (its the blue one)

#define LED_STRIP_1 26
#define LED_STRIP_2 27
#define LED_STRIP_3 14

#define ENC_1 36
#define ENC_2 39
#define ENC_3 34

#define ADC_SELECT 23
#define ADC_RX 19
#define ADC_TX 18

#define MOTOR_1 15
#define MOTOR_1_RMT_CHANNEL 3
#define MOTOR_2 33
#define MOTOR_2_RMT_CHANNEL 4
#define MOTOR_3 25
#define MOTOR_3_RMT_CHANNEL 5

#define CONTROLLER_SERIAL Serial2

#define ADC_SELECT 23
#define ADC_RX 19
#define ADC_TX 18

// ---- MISC ----

#define ADAFRUIT_RMT_CHANNEL_MAX 3 // LED strips can use 3 RMT channels 0 - 2

#endif

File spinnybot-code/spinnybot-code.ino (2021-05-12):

/************************************************************************/ /**
*@file
*@brief The main code to load onto the NRC 2021 battle bot
*
*TO DO
* impliment 12v sense and satus led
* debug
***************************************************************************/

#include <math.h>
#include <FastLED.h>
#include <SPI.h>
#include "Nidec24hController.h" // https://github.com/sdsmt-robotics/MotorSpeedController/tree/master/Software/controllerInterfaceLib
#include "Controller.h"         // https://github.com/sdsmt-robotics/Controller/tree/master/Code/receive
#include "Imu.h"
#include "LedStrip.h" 

/*********************Pin labels***********************
 * GPIO 0 SS for the slave motor 3
 * GPIO 1 
 * GPIO 2 12V sense (ADD)
 * GPIO 3 
 * GPIO 4 SS for the slave motor 2
 * GPIO 5 SS for the slave motor 1
 * GPIO 6
 * GPIO 7
 * GPIO 8
 * GPIO 9
 * GPIO 10
 * GPIO 11
 * GPIO 12
 * GPIO 13
 * GPIO 14
 * GPIO 15
 * GPIO 16 Tx0 for serial to the xBee REQ
 * GPIO 17 Rx0 for serial to the xBee REQ
 * GPIO 18 SCK SPI to the motor boards REQ
 * GPIO 19 MISO SPI to the motor boards REQ
 * GPIO 20
 * GPIO 21
 * GPIO 22
 * GPIO 23 MOSI SPI to the motor boards REQ
 * GPIO 24
 * GPIO 25 for the led strips 3
 * GPIO 26 for the led strips 1
 * GPIO 27 for the led strips 2
 * GPIO 28
 * GPIO 29
 * GPIO 30
 * GPIO 31
 * GPIO 32
 * GPIO 33 status LED (ADD)
 * GPIO 34
 * GPIO 35
 * GPIO 36 
 * GPIO 37
 * GPIO 38
 * GPIO 39
 ***************************************************/

//**********constants for the motors**********
const float rotation = 400; // Chassis rotation speed in RPM
const float translation = 2.5; // Driving feet per sec 
const float chassisRad = 5.25; // Chassis radius in inches
const float wheelRad = 1.18; // Wheel radius in inches
const float translateSpeed = translation / wheelRad * (12 * 60 / 2 / PI);
const float rotationSpeed = rotation * chassisRad / wheelRad;
const float fullPower = 1000; // Power to run at when going full speed

//**********motor objects**********

// Pin for motor slaves
#define MOTOR_PIN_1 5
#define MOTOR_PIN_2 4
#define MOTOR_PIN_3 0

// Pins for data to led strip
#define DATA_PIN_1 25
#define DATA_PIN_2 26
#define DATA_PIN_3 27

#define IMU_PIN  22

// Motor Controller class
Nidec24hController motor1(SPI, MOTOR_PIN_1);
Nidec24hController motor2(SPI, MOTOR_PIN_2);
Nidec24hController motor3(SPI, MOTOR_PIN_3);


//**********IMU*************************
const float IMU_OFFSET = PI/3; // Angle IMU is facing relative to front of robot
Imu orientation(IMU_PIN);

//**********Controller object and key binding**********

//Create the communications object. Use Serial for the communications.
Controller controller(Serial2);

#define START_BUTTON UP //button
#define STOP_BUTTON DOWN //button
#define DRIVE_JOYSTICK LEFT //joystick
#define TURN_JOYSTICK RIGHT //joystick
#define PHASE_LEAD  RIGHT //button
#define PHASE_LAG   LEFT //button
#define SPEED_UP    RIGHT //trigger
#define SPEED_DOWN  LEFT //trigger
#define FULL_SEND   RIGHT //trigger

//**********constants for the LEDs**********

//the number of adressible horizontal stripes of leds around the robot
const int bot_resolution = 50;

// How many leds in your strip?
#define NUM_LEDS 8

// Define LED Strip angles
const float stripOffset = 0.0;  // Offset for the #1 LED Strip
float stripAngles[] = {0.0 + stripOffset,
                       2*PI/3.0 + stripOffset,
                       4*PI/3.0 + stripOffset};

// Led strips setting managers
LedStrip ledStrip1;
LedStrip ledStrip2;
LedStrip ledStrip3;

// Temps for calculating strip colors
CRGB stripColors[] = {CRGB::Red, CRGB::Red, CRGB::Red};

//the number of addressable radial led's per horizontal stripe
//CRGB leds[NUM_LEDS*3];

//const float screen_step = (2 * PI) / float(bot_resolution);

const float stripEpsilon = (2 * PI) / 60.0;

//construct screens(class is a work in progress)
//screen main_screen(bot_resolution, NUM_LEDS, bot_resolution);

//**********DATA for the LEDs********** (continued in setup)
//these arrays contain all data for static led patterns and simple 
//animations not defined by a helper function

/*CRGB red[NUM_LEDS];
CRGB orange[NUM_LEDS];
CRGB yellow[NUM_LEDS];
CRGB green[NUM_LEDS];
CRGB blue[NUM_LEDS];
CRGB purple[NUM_LEDS];*/

//**********Other global vars and consts**********

const bool debug = false;
const bool debug_orientation = false;
const bool debug_motor_speeds = false;
const int debug_level = 4; //0 to 4
const bool use_led = true;

bool fullSend = false;  // Toggle to full power mode
bool flipped = false;


//**********setup**********
/** ***************************************************************************
* @par Setup:
* Sets up any objects that need initialization, makes tests for valid
* configurations, and finds global variables that then remain constant throughout
* the rest of the code.
*
 *****************************************************************************/
void setup()
{
    //generic counter var
    int i = 0;
    int j = 0;

    delay(5000);

    // start serial if debug is true
    if (debug)
    {
        //wait for serial to connect
        Serial.begin(115200);
        while (!Serial && debug)
        {
        }
    }

    if (debug)
    {
        Serial.println("Serial start");
    }

    //**********LED screen setup**********
    // Offset angles for spinning
    for (int i = 0; i < 3; i++) {
      stripAngles[i] = normalizeAngle(stripAngles[i]);
    }

    // Fast LED stuff
    FastLED.addLeds<NEOPIXEL, DATA_PIN_1>(ledStrip1.getPixelData(), NUM_LEDS); // GRB ordering is assumed
    FastLED.addLeds<NEOPIXEL, DATA_PIN_2>(ledStrip2.getPixelData(), NUM_LEDS); // GRB ordering is assumed
    FastLED.addLeds<NEOPIXEL, DATA_PIN_3>(ledStrip3.getPixelData(), NUM_LEDS); // GRB ordering is assumed
    FastLED.setBrightness(50);

    // Show initial color
    ledStrip1.fillColor(CRGB::Yellow);
    ledStrip2.fillColor(CRGB::Yellow);
    ledStrip3.fillColor(CRGB::Yellow);
    FastLED.show();
    
    //re add test
    
    
    //**********SPI setup**********
    // Initialize the SPI communications
    SPI.begin();
    SPI.setClockDivider(SPI_CLOCK_DIV32);

    if (debug && Serial.println("SPI start"))
    {
    }

    //**********motor setup**********
    if (debug && Serial.println("Motor init...")) { }
    // Initialize the motor control
    motor1.init();
    motor2.init();
    motor3.init();

    motor1.brake();
    motor2.brake();
    motor3.brake();

    if (debug && Serial.println("Motor init done.")) { }
    
    //**********imu initialization**********
    if (debug && Serial.println("Initializing IMU...")) { }
    while (!orientation.init())
    {
        if (debug && Serial.println("Failed to initialize IMU!")) { }
        delay(1000);
    }
    orientation.setOffset(IMU_OFFSET);

    if (debug && Serial.println("IMU init complete.")) { }

    ledStrip1.fillColor(CRGB::Green);
    ledStrip2.fillColor(CRGB::Green);
    ledStrip3.fillColor(CRGB::Green);
    FastLED.show();
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

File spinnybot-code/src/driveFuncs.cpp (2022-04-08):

#include "driveFuncs.h"
#include "utility.h"

/**
 * Constructor for the class.
 */
DriveManager::DriveManager() : filter(100, 100, 0.08) {}


/**
 * Estimate the bot's angular velocity.
 * 
 * @param encoders - Array of encoders on the bot.
 * @param numEncoders - Number of encoders
 * @return The estimated bot velocity
 */
float DriveManager::estimateBotVelocity(float mtrVels[NUM_MTRS], bool encGood[NUM_MTRS]) {
    float sum = 0;
    unsigned numSummed = 0;
    for (int i = 0; i < NUM_MTRS; i++) {
        if (encGood[i]) {
            sum += mtrVels[i];
            numSummed++;
        }
    }

    // Invert wheel velocity if spinning in this mode (upright)
    if (spinnigCW) {
        sum *= -1;
    }

    return (numSummed == 0 ? 0 : sum * WHEEL_RADIUS / float(numSummed * BOT_RADIUS));
}

/**
 * Update orientation estimation.
 * 
 * @param imuVelocity - Angular velocity from IMU. In rad/s.
 * @param encVelocities - Array of velocity values from encoders. In rpm.
 * @return Angle estimate.
 */
float DriveManager::updateOrientation(float imuVelocity, float encVelocities[3]) {
    unsigned long lastUpdate = micros();
    static float lastAngle = curAngle;

    // Time delta for integrating
    unsigned curTime = micros();
    float deltaT = (curTime - lastUpdate) * 0.000001;
    lastUpdate = curTime;

    // Remove bad encoder values. Assume good if nonzero or if all are zero.
    bool encGood[3] = {0};
    bool allZero = true;
    for (int i = 0; i < 3; i++) {
        bool encZero = isZero(encVelocities[i]); 
        encGood[i] = !encZero;
        allZero = allZero && encZero;
    }
    // If all are zero, assume all are good
    if (allZero) {
        memset(encGood, 1, sizeof(bool)*3);
    }

    // Estimate velocity using encoder values
    float encVelocity = estimateBotVelocity(encVelocities, encGood) * RPM_TO_RAD_SEC;

    // Invert IMU velocity if needed (it is upside-down)
    if (spinnigCW) {
        imuVelocity *= -1;
    }

    // Fuse velocity values together in a semi-intelligent manner
    // TODO: will have to re-think this if adding accel gyros
    if (encVelocity < 500) {
        // Low speed mode
        velocityEst = 0.25 * encVelocity + 0.75 * imuVelocity;
    } else {
        // High speed mode
        velocityEst = encVelocity;
    }

    // Filter
    velocityEst = filter.updateEstimate(velocityEst) * driftComp;

    // Update angle estimate. 
    integrate(velocityEst, deltaT);

    // Heading estimation
    if (translateStarted) {
        // Check if we have crossed a boundary (sign change)
        if ((curAngle < 0) != (lastAngle < 0)) {
            // Start udpating heading if we have done at least two cycles with translation
            if (translateCycleCount >=2) {
                // Update heading and translation offset
                heading = normalizeAngle(maxSpeedAngle + (maxMtrSpeed > 0 ? HALF_PI : -HALF_PI));
                translateOffsetAngle += angleTo(commandDir, heading, !spinnigCW) * 0.5;
            } else {
                translateCycleCount++;
            }
            maxMtrSpeed = 0;
            maxSpeedAngle = 0;
        }

        // Track the max speed
        for (int i = 0; i < 3; i++) {
            if (encGood[i] && abs(encVelocities[i]) > abs(maxMtrSpeed)) {
                maxMtrSpeed = encVelocities[i];
                maxSpeedAngle = curAngle + MTR_OFFSETS[i];
            }
        }
    }

    return curAngle;
}

void DriveManager::setInverted(bool inverted) {
    spinnigCW = !inverted;
}

bool DriveManager::isInverted() {
    return !spinnigCW;
}

/**
   @brief Updates drive motor powers with control and angle inputs.
   @param power array of power values for motors.
   @param spin Spin speed modifier. -1.0 to 1.0
   @param x X direction movement modifier. -1.0 to 1.0
   @param y Y direction movement modifier. -1.0 to 1.0
   @param angle Current angle of robot in radians
*/
void DriveManager::calcDrivePower(int power[3], float spin, float x, float y) {
    // TODO: Set direction of spinning based on spinning dir var
    spinnigCW = spin > 0;

    // Handle translation offset updating
    if (!(abs(x) > 0.001 || abs(y) > 0.001)) { // Not translating
        translateStarted = false;
    } else if (!translateStarted) { // Translation starting
        translateCycleCount = 0;
        translateOffsetAngle = (spinnigCW ? 1 : -1) * HALF_PI * spin;  // Add an initial guess for drift compensation
        translateStarted = true;
    }

    // constrain inputs to prevent problems with math
    spin = constrain(spin, -1.0, 1.0);
    x = constrain(x, -1.0, 1.0);
    y = constrain(y, -1.0, 1.0);

    float spin_power = 0;
    float trans_power = TRANS_MAX_POWER * sqrtf((x * x) + (y * y));
    commandDir = atan2f(y, x) - HALF_PI; // Rotate because forward on controller is (x=0, y=1).
    
    float comp_angle = commandDir - curAngle + translateOffsetAngle;

    if (spin > 0) {
        // robot upright
        spin_power = SPIN_MIN_POWER + ((SPIN_MAX_POWER - SPIN_MIN_POWER) * spin);

        power[0] = (spin_power + (trans_power * sinf(MTR_OFFSETS[0] - comp_angle)));
        power[1] = (spin_power + (trans_power * sinf(MTR_OFFSETS[1] - comp_angle)));
        power[2] = (spin_power + (trans_power * sinf(MTR_OFFSETS[2] - comp_angle)));

    } else if (spin < 0) {
        // robot fliped over
        spin_power = -SPIN_MIN_POWER + ((SPIN_MAX_POWER - SPIN_MIN_POWER) * spin);

        power[0] = (spin_power + (trans_power * sinf(MTR_OFFSETS[0] + comp_angle)));
        power[1] = (spin_power + (trans_power * sinf(MTR_OFFSETS[1] + comp_angle)));
        power[2] = (spin_power + (trans_power * sinf(MTR_OFFSETS[2] + comp_angle)));
    }
}

/**
 * Integrate the velocity value over the given time period to update the angle estimate.
 * 
 * @param deltaT - Time that has elapsed since the last sample
 */
void DriveManager::integrate(float velocity, float deltaT) {
    static float lastVal = velocity;
    
    // Trapezoidal approximation
    curAngle = normalizeAngle(curAngle + (velocity + lastVal) / 2 * deltaT);

    lastVal = velocity;
}

/**
 * Get the current bot angle estimate.
 * 
 * @return the current angle estimate.
 */
float DriveManager::getCurAngle() {
    return curAngle;
}

/**
 * Get the current bot heading estimate. Only accurate if translating.
 * 
 * @return the current heading estimate.
 */
float DriveManager::getCurHeading() {
    return heading;
}

/**
 * Rotate "forward" direction by the given delta.
 * 
 * @param delta - Amount by which to rotate in rads.
 */
void DriveManager::rotate(float delta) {
    if (!isZero(delta)) {
        curAngle += delta;
        translateCycleCount = 0; // Reset the heading calculation cause it will be all kinds of screwed up
    }
}

/**
 * Adjust the drift compensator multiplier. The multiplier is 1.0 by default.
 * 
 * @param delta - Amount to chage by.
 */
void DriveManager::adjustDrift(float delta) {
    if (!isZero(delta)) {
        driftComp += delta;
    }
}

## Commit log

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2020-02-08 Switched the motor object over to the new motor driver and commented out IMU code
2020-02-09 Fixed motor objects.
2020-02-15 Fixed kiwi drive for new motor controllers.
    [nrc-basic-kiwi-drive.ino]
2020-02-16 Added the "slave" files for offloading the motor encoder processing to a "slave" Arduino.
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2021-02-14 Deleted old and unnecessary code code for old hardware and added the new IMU and LED code.
2021-02-14 Removed unnecessary code and libraries from the old kiwi-drive code. The new IMU and LED code will be moved to this file. In addition, the code will be modified to use sams motor controller library a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
2021-02-17 Added the xBee controller receive code to replace the PS3 code used for testing.
    [nrc-kiwi-drive.ino]
2021-02-26 Fixed the POV_desplay class so that it both compiles and the number of leds can be easily changed. Some rework needs to be done for the screen class to be safe to use in the final application, i.e. p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
    [nrc-kiwi-drive.ino]
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2021-03-19 Separated the IMU code out into its own class and simplified the main drive code accordingly.
2021-03-19 Fixed several bugs related to the implementation (Temporarily removed POV display code).
    [nrc-kiwi-drive.ino]
2021-03-20 Added the simple Kalman filter to the BB_IMU code. Added an modifiable offset to the BB_IMU code and made the relevant changes in the kiwi drive code. Cleaned up the kiwi drive code.
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2021-03-27 fixed bug in the code because apparently semicolons are important.
    [nrc-kiwi-drive.ino]
2021-03-28 Added the ability to speed up or slow down the bot based on the controller state. This amplification is currently set at +- 50%.
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2021-03-30 Split the controller updates and motor speed calculations off into separate functions.
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2021-04-10 add kicad files for mainboard
    [spinnybot-motherboad-B_Cu.gbr, spinnybot-motherboad-B_Mask.gbr, spinnybot-motherboad-B_Silks.gbr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]
2021-04-10 pcb layout
    updated the pcb circuit diagram with some changes in parts etc.
    [spinnybot-motherboad.kicad_pcb, spinnybot-motherboad.kicad_sch]
2021-04-11 worked on redesigning the pcb design for the new shape
    [spinnybot-motherboad.kicad_pcb]
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2021-04-27 board rev 2, got all components placed. still need to route
    [mcu_buffers.kicad_sch, sheet2.kicad_sch, spinnybot-motherboad.kicad_pcb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]
2021-04-29 routed rev2 mainboard
    [mcu_buffers.kicad_sch, spinnybot-motherboad.kicad_pcb, spinnybot-motherboad.kicad_sch]
2021-04-29 added graphics and generated gerbers
    [spinnybot-motherboad-B_Cu.gbr, spinnybot-motherboad-B_Mask.gbr, spinnybot-motherboad-B_Silks.gbr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]
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2021-05-01 Updated the code to use the new IMU (This code has not been debuged or tested on the hardware so there are probably tons of problems).
    [nrc-kiwi-drive.ino]
2021-05-01 Fixed pin assignment.
2021-05-08 added PDF schematic and fixed a routing error
    [spinnybot-motherboad.kicad_pcb, spinnybot-motherboad.kicad_sch]
2021-05-12 Fix issue with missing library
    [spinnybot-code.ino]
2021-11-18 Replaced transistor symbols and footprints with correct ones.
    [mcu_buffers.kicad_sch, spinnybot-motherboad.kicad_pcb, spinnybot-motherboad.kicad_sch]
2022-02-06 split schematic into multiple files and stole Erick's homework on redoing the power button
    [connectors.kicad_sch, mcu_buffers.kicad_sch, power.kicad_sch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]
2022-02-06 fixed some reference designators so the layout isn't broken
    [connectors.kicad_sch, mcu_buffers.kicad_sch, power.kicad_sch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]
2022-02-10 Changed values for power RC circuit
    [power.kicad_sch, spinnybot-motherboad.kicad_sch]
2022-02-17 Removed buck converter PS1, voltage sense divider, and motor connections. Added encoder connectors
    [connectors.kicad_sch, power.kicad_sch, spinnybot-motherboad.kicad_sch]
2022-02-19 Added ESC connections
    [connectors.kicad_sch, power.kicad_sch, spinnybot-motherboad.kicad_sch]
2022-02-26 Made and imported ESC footprint, added 10 pin JST connector symbol and footprint, updated Q2 FET to control ESC power
    [connectors.kicad_sch, power.kicad_sch, spinnybot-motherboad.kicad_sch]
2022-02-27 add accelerometers, ADCs, and UART multiplexer
    [imu-accelerometers.kicad_sch, mcu_buffers.kicad_sch, power.kicad_sch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]
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2022-02-27 fix broken file after merge
    [spinnybot-motherboad.kicad_sch]
2022-03-03 removed some old signals
    [mcu_buffers.kicad_sch, power.kicad_sch, spinnybot-motherboad.kicad_sch]
2022-03-03 Made ESP32 connections, added logic level shifter
    [connectors.kicad_sch, mcu_buffers.kicad_sch, power.kicad_sch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]
2022-03-05 PCB schematic (hopefully) finished
    [connectors.kicad_sch, imu-accelerometers.kicad_sch, mcu_buffers.kicad_sch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]
2022-03-05 Added 4 pin JST connector footprint and assigned footprints
    [connectors.kicad_sch, imu-accelerometers.kicad_sch, mcu_buffers.kicad_sch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]
2022-03-06 Started board layout
    [connectors.kicad_sch, power.kicad_sch, spinnybot-motherboad.kicad_pcb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]
2022-03-08 Continued adding to board layout, added missing ESC connector footprint
    [connectors.kicad_sch, mcu_buffers.kicad_sch, power.kicad_sch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]
2022-03-09 Most of the parts on the board, still missing battery connections
    [spinnybot-motherboad.kicad_pcb]
2022-03-10 Power pads added, beginning routing
    [power.kicad_sch, spinnybot-motherboad.kicad_pcb, spinnybot-motherboad.kicad_sch]
2022-03-11 Finishing routing board, needs checking over to make sure everything looks good
    [power.kicad_sch, spinnybot-motherboad.kicad_pcb, spinnybot-motherboad.kicad_sch]
2022-03-11 Added chip names and solder jumper instructions
    [spinnybot-motherboad.kicad_pcb]
2022-03-12 Addressed Pratik's concerns about cap placement and missing caps
    [imu-accelerometers.kicad_sch, mcu_buffers.kicad_sch, spinnybot-motherboad.kicad_pcb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]
2022-03-12 PCB design rule checker fixes, silkscreen overlaps and self-intersecting courtyards
    [spinnybot-motherboad.kicad_pcb]
2022-03-12 fix LEDSTRIP_GND on the FET not being connected
    [power.kicad_sch, spinnybot-motherboad.kicad_pcb, spinnybot-motherboad.kicad_sch]
2022-03-13 tweaks to routing to make the ground plane more connected, add a top copper ground pour. move ESC FET.
    [mcu_buffers.kicad_sch, power.kicad_sch, spinnybot-motherboad.kicad_pcb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]
2022-03-13 add a couple ground test points
    [power.kicad_sch, spinnybot-motherboad.kicad_pcb, spinnybot-motherboad.kicad_sch]
2022-03-13 swap out motor active indicator FET for a BJT we already have
    [power.kicad_sch, spinnybot-motherboad.kicad_pcb, spinnybot-motherboad.kicad_sch]
2022-03-13 add more no-connect flags to schematic
    [imu-accelerometers.kicad_sch, mcu_buffers.kicad_sch, power.kicad_sch]
2022-03-13 adjust mounting holes to have pads and change locations
    [imu-accelerometers.kicad_sch, mcu_buffers.kicad_sch, power.kicad_sch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]
2022-03-13 silkscreen fix, add 'THIS BOARD WORKS'
    [spinnybot-motherboad.kicad_pcb]
2022-03-13 change solder mask to purple
    [spinnybot-motherboad.kicad_pcb]
2022-03-13 add 3d models, silkscreen fixes
    [spinnybot-motherboad.kicad_pcb]
2022-03-13 move encoder cable strain relief holes
    [spinnybot-motherboad.kicad_pcb]
2022-03-13 DRC fixes
    [spinnybot-motherboad.kicad_pcb]
2022-03-13 move ESC FET
    [spinnybot-motherboad.kicad_pcb]
2022-03-14 add extra strain relief holes back in the original locations
    [power.kicad_sch, spinnybot-motherboad.kicad_pcb, spinnybot-motherboad.kicad_sch]
2022-03-14 adjust board to use new outline with bottom edge closer to center
    [spinnybot-motherboad.kicad_pcb, spinnybot-motherboad.kicad_sch]
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2022-03-28 possibly fix leds untested
    [main.cpp]
2022-03-29 confirmed serial1 pin swap worked
    [accelerometer.cpp, accelerometer.h, main.cpp]
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2022-04-04 Add encoder test code and fix some bugs
    [AS5134.cpp, controller_test.cpp, encoder.cpp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]
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2022-04-05 fixed imu code
2022-04-05 Updated voltage divider on power circuit
    [mcu_buffers.kicad_sch, power.kicad_sch, spinnybot-motherboad.kicad_sch]
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2022-04-07 Fix drive code (hopefully)
    [driveFuncs.cpp, driveFuncs.h, drive_test.cpp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]
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

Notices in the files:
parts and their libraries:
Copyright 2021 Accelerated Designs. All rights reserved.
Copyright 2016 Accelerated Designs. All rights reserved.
